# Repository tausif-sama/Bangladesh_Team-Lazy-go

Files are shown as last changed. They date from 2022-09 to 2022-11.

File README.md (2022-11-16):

# Engineering Documentation | Team Lazy-go | Bangladesh
----

This repository contains engineering materials of Lazy-bot, a self-driven vehicle's model from Team Lazy-go, Bangladesh, participating in the WRO Future Engineers competition in the season 2022.

----

## Team Members:

- Tausif Samin - email: <tausifsamin.dhk@gmail.com>, Discord: Ikigai#8742
- Iqbal Samin Prithul - email: <prithul0218@gmail.com>, Discord: Prithul#3957

----

## Repository Overview

+ `chassis` - this folder contains details of the chassis that we've used
+ `models` - contains 3D Printable files designed by us
+ `schemes` - contains the electrical systems schematics 
+ `src` - contains the main programs and control software and 
+ `t-photos` - contains one serious and one funny photo
+ `v-photos` - contains the photos of the robot from all required directions
+ `video` - contains youtube link of the video where you can see our robot in action
+ `others` - other essential photos

----

# Program arrangement and Algorithm Planning

The robot is running on an ESP32-based development board called the JRC board locally made in our country to run all the actuators and sense the environment. It is using the Huskylens to see the red/green obstacles as well as the corner lines (blue/orange). An MPU6050 gyroscope and accelerometer sensor are used to detect the orientation of the robot and count laps.

When the robot is first powered on with the battery, it initializes the chip and starts communicating with the Huskylens and IMU sensor. Once it is ready, the servo motor gets centered and it waits for the user to push the button. The code is then divided into three major parts - 

### Part 1 - Detecting run direction:

The first part determines the direction of the robot run. The robot moves slowly through the first straightforward section to ensure it can safely detect the direction of the run with its sonar sensors. Once it detects a large distance (>90cm) from one of the sensors, it marks the direction as “L” - clockwise, or “R”  - anti-clockwise accordingly.

### Part 2 - Completing the run as fast as possible:

In this part, we run a PID loop (1st round) or a proportional+obstacle avoiding code(2nd round) to complete the run as fast as possible. 

### **Wall avoidance:**

In the first round, we only check the sonar on the inner wall side (based on the direction of run detected from Part 1) to run a PID (proportional, integral, derivative) code. The code tries to keep the robot at a fixed distance from the wall while slowing down the rear axle drive motor whenever a turn is initiated.
To complete this part as fast as possible, we use smart algorithms to detect when the robot has just finished a turning section and is about to enter a straight section. The robot then spins the drive motor at maximum speed for a short period of time (40-50mS) to give the robot a great acceleration or “boost”.

In the 2nd round, however, we decided to disable the boost and changed PID control to just P or proportional to keep the robot centered on the track, which is sufficient at the slow speed of the robot.

### **Obstacle avoidance:**

When the huskylens detects an object, the ESP32 gets the object's color and location in the X and Y axis, as well as its height (to get the distance). The robot then follows the obstacle with an offset. Meaning it follows slightly on the right side of red obstacles, and slightly to the left of green obstacles. And once it reaches a distance of less than 30 cm, it turns the front wheel proportionally to the distance of the object (calculated from height) and the position of the object on the screen's horizontal axis.

### Wall collision protection:

If the robot detects a wall within 8cm of one of the sides, it rotates the servo in the other direction for a few milliseconds to keep the robot from hitting the wall.

### Part 3 - Detecting the end of 3 laps:

The robot equips a gyroscope sensor to measure the yaw angle by integrating the rotational acceleration values on the Z axis over time. Gyroscope sensors are infamous for drift in the angle over time, but our robot runs for such a short time that it does not affect its performance.

When the start button is pressed, the robot is at a zero-degree angle starting position. After each lap of the track, the robot spins 360 degrees. So we can detect the completion of three laps as soon as the robot completes 3x360 or 1080 degrees turn (+/- 20 degrees to compensate for errors). 
However, the robot is not instantly stopped, since it may not have reached the straightforward section. We start waiting for the Huskylens to detect a blue or orange line in front of it and stop instantly with a short backward pulse to the drive motor (hard break).

----

# Electrical Systems Design

We've carefully selected the best possible parts for our robot after several hundred hours of R&D and have tried to achieve highest possible efficiency and reliability. The electrical systems design is explained in the following paragraph.

## Parts List

+ JRC Board: An ESP32 based development board (Made in Bangladesh)
+ Huskylens: Embedded Vision Sensor
+ Adafruit HC-SR04 Ultrasonic Sensors
+ 12V 300RPM DC Geared Motor
+ 9imod DS20MG Servo Motor
+ VNH2SP30 Motor Driver
+ MPU6050
+ 2x MP1584 Buck Converter
+ Pololu U3V70A Boost Converter
+ 3S LiPo battery input through XT60 Connector

## Design decisions

+  JRC Board
    - We're using the JRC Board as it is equipped with an ESP-32 microcontroller at a clock speed of 240Hz. This is the fastest development platform for the price currently available. As the ESP-32 is dual-core, we can run two loops simaltaneously which is very benificial. 
    - There's a brief but impressive backsotry of the JRC Board. The abbreviation of 'JRC' is Jamilur Reza Chowdhury. Dr. Jamilur Reza Chowdhury was a Bangladeshi Civil Engineer, Professor, Researcher, and Education Advocate. He is also the pioneer of computers in Bangladesh and brought the first ever computers in Bangladesh. This board was designed and developed in the memory of Dr. Jamilur Reza Chowdhury to spread the light of IoT and hardware level electronics education to kids in Bangladesh.
- We're using the Huskylens which is an embedded machine vision sensor based on Kendryte K210 that can recognize and track colors and objects in real-time. We're using I2C to receive tracked color position data.
- We're using a 12V 500RPM geared motor with a modified gearbox that provides ample Torque and Speed to drive our car weiging about 900g.
- The front Axel is being articulated by a 9imod DS20MG Servo Motor. This Servo boasts a coreless motor inside and operates at a speed of 0.09sec/60°@7.4V.
- We've used a VNH2SP30 Motor driver replacing a TB6612FNG because of lack of current. VNH2SP30 has no problems communicating with the 3.3v ESP-32 and provides ample current to the motor.
- We're using 2x HC-SR04 sonar sensors to measure distance from both the left and right walls.
- The Pololu U3V70A Boost Converter was used because providing sustained voltage to the motor driver is an absolute necessity for achieving consistent performance. U3V70A Provides a constant 12v to the Motor driver regardless of the battery voltage.
- 2x MP1584 buck converters were used, one for powering all the 5v peripherals and on-board devices and the other one for providing 7.4v to the servo motor.
- A MPU6050 was used to know the orientation of the robot in real-time. This data is later used to count laps.
- A 3S 12.6V 1500mAh battery is powering this entire system. We're getting a runtime of average 3 hours.

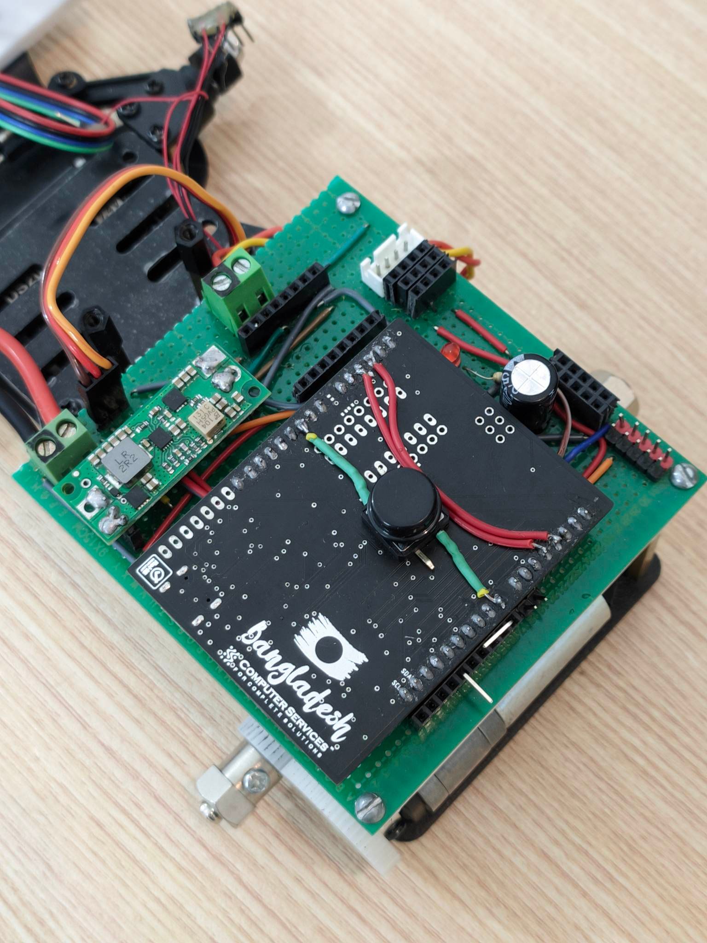
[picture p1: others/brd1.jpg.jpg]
brd1

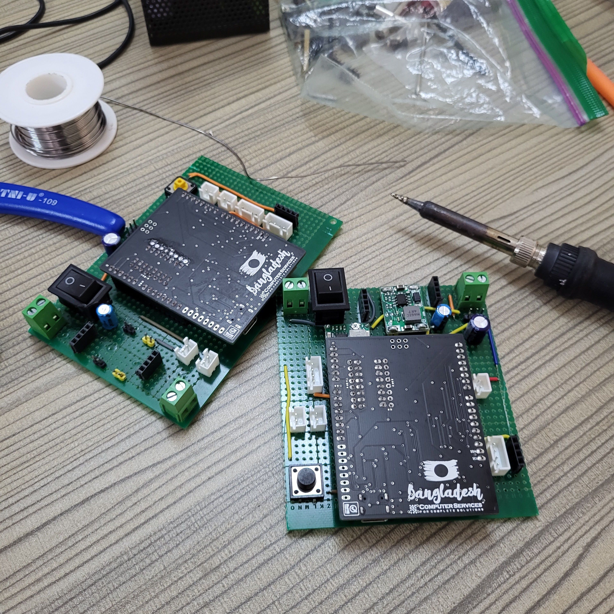
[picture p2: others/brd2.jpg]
brd2


----

# Mechanical Design

We're using a ready made Ackermann based chassis kit from YF robot and have significantly modified each aspect of the chassis. The chassis base plate is made of Aluminum and the rest of the parts involve brass spacers, acrylic top plates, front articulating axel parts and some other miscellaneous parts. We've also designed and 3D Printed some parts for making our chassis more practical.

## Design Decisions
We setteled on the YF Robot chassis because it provided a robust platform to work on and featured ackermann steering mechanism. We've deigned and 3D printed some parts which were required for the optimal operation of the robot. 

## 3D Printed parts designed by us

- We've designed a sonar mount which is mounted in the front of the robot where the sonar sensors are mounted at an angle of 20 deg. We've tested this to be the optimal angle for the sonars to detect walls before hand, providing ample time for the bot to react.
- An elevated and angled mount for the huskylens was designed for the camera to get optimal vision of the track.
- The wheels were completely 3D printed, except for the tires. After extensive testing, we've found that thin twheels perfom better in cases where precise movement is required.
- A mounting plate for the veroboard was designed so that the solder joints under the board do not make any contact with the motor.

----

# Software Setup
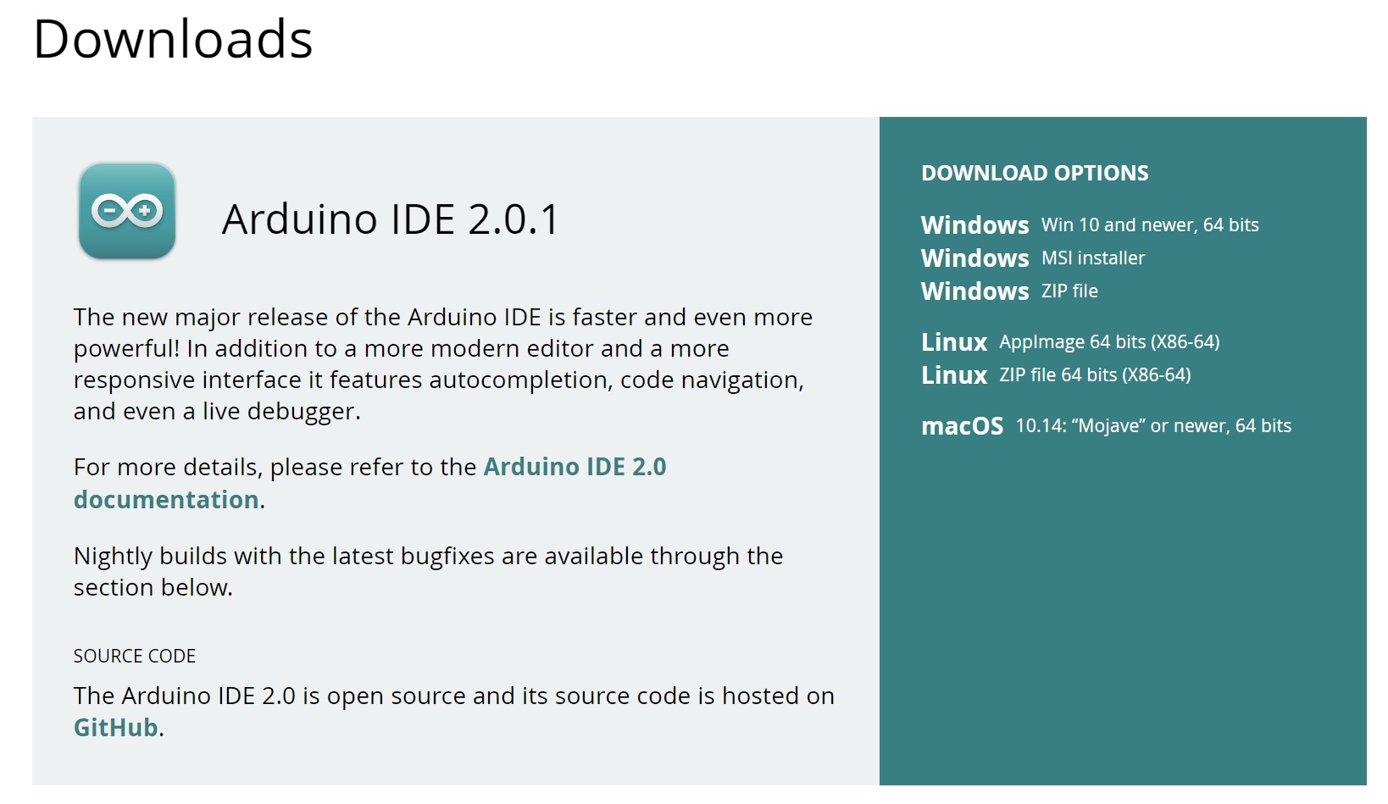
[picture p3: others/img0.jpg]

- First we need to install the latest Arduino IDE on our computer from: arduino.cc/en/Main/Software. If you already have an older version, uninstall it and install the latest one again. Otherwise, it may not work.

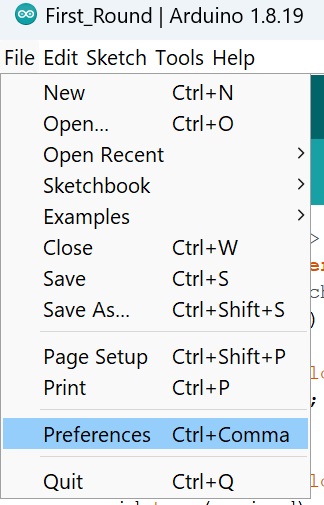
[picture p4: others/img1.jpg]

- In your Arduino IDE, go to File > Preferences, and enter the following into the "Additional Board Manager URLs" field, and click OK:
`https://raw.githubusercontent.com/espressif/arduino-esp32/gh-pages/package_esp32_index.json`

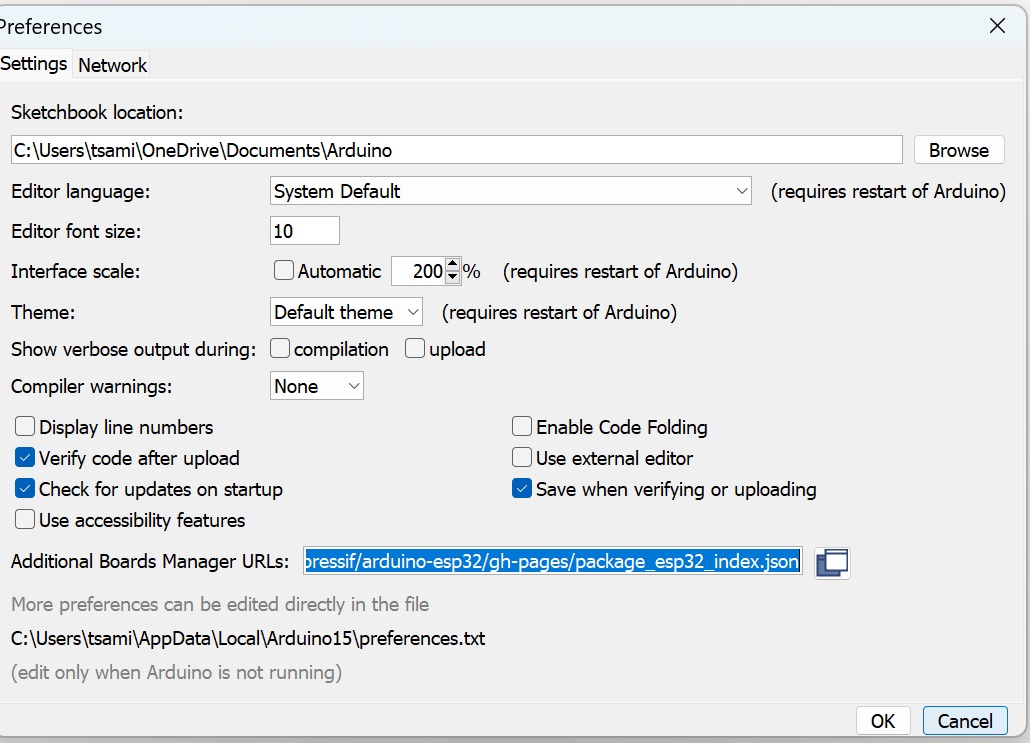
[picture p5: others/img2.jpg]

- Open the Arduino Boards Manager: Tools > Board > Boards Manager... and search for ESP32. Press install button for the "ESP32 by Espressif Systems".

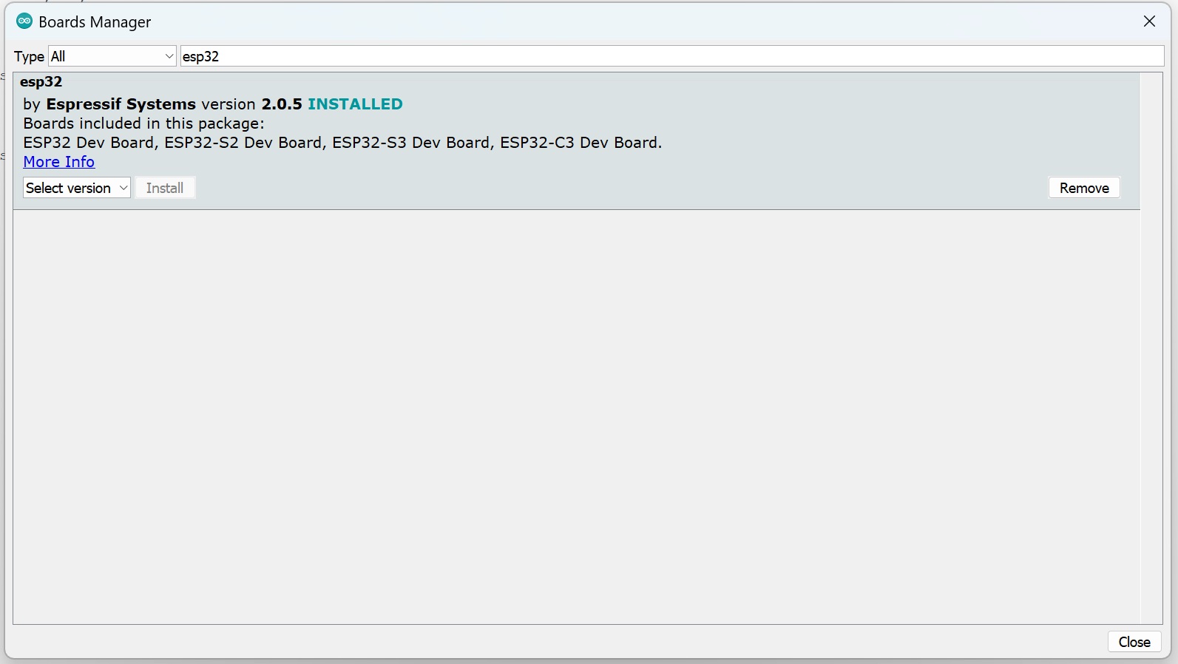
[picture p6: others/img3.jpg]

- Now we try to upload our code to the ESP32. Select your Board in Tools > Board menu (in our case it is the DOIT ESP32 DEVKIT V1).

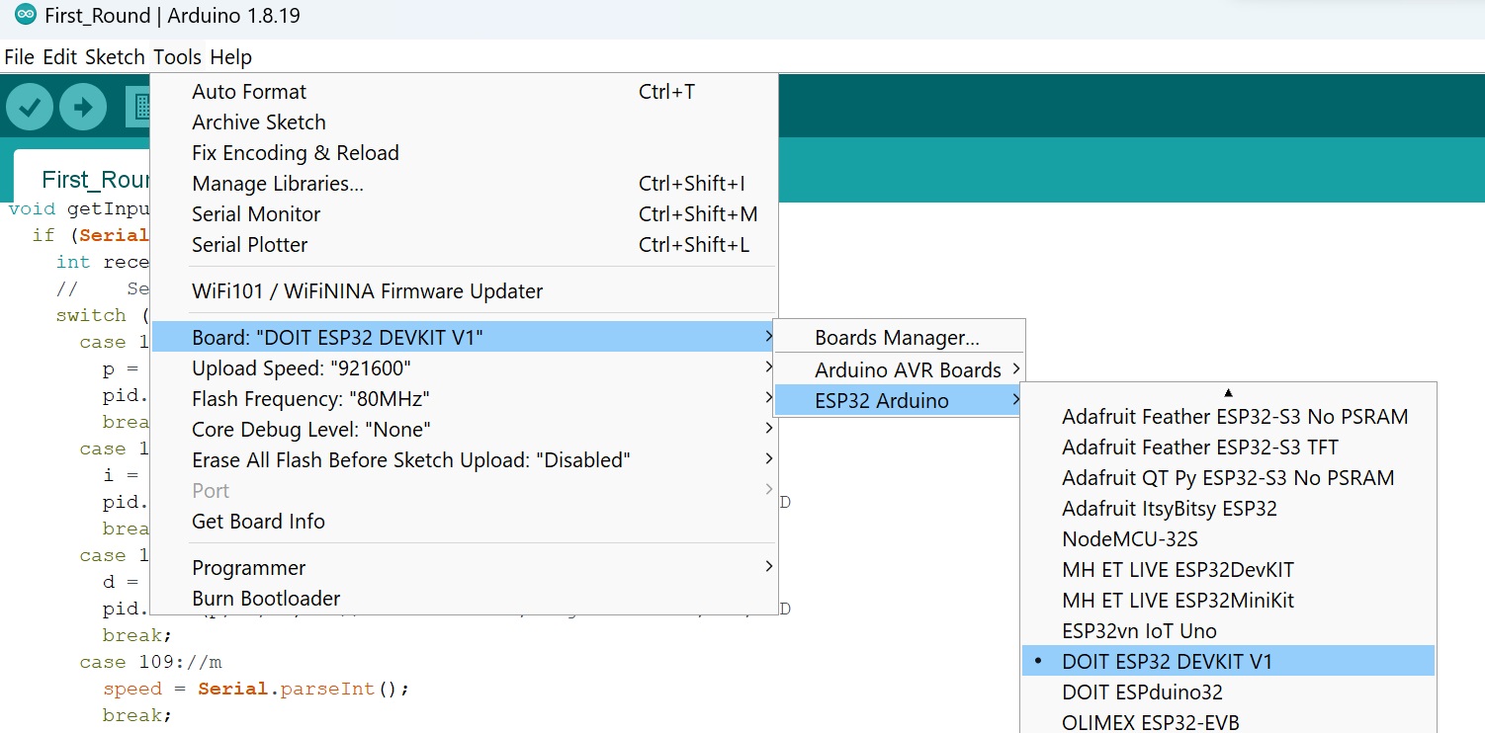
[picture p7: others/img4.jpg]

- Select the COM port, and open the sketch.

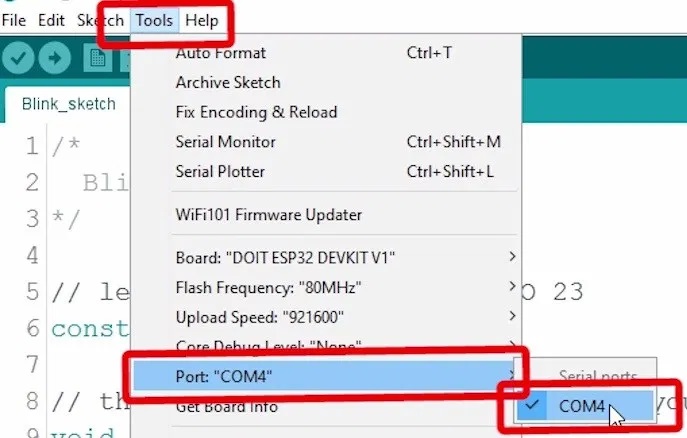
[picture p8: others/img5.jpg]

- Press the Upload button in the Arduino IDE. Wait a few seconds while the code compiles and uploads to your board. It should say "Done Uploading" if the upload completes successfully.

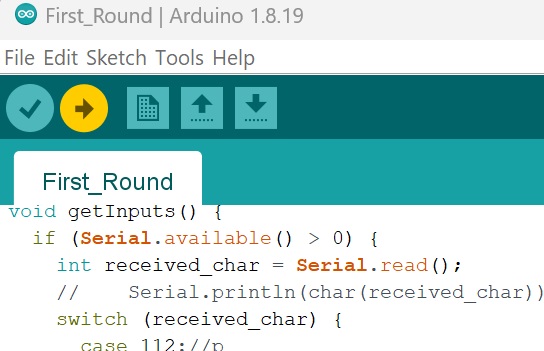
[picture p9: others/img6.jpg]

- Now you can place the robot on the track, power it up, and wait until the front servo centers.

- Press the button and it will start doing the laps.

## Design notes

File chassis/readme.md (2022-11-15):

Main Chassis 
====

We're using a ready made Ackermann based chassis kit from YF robot and have significantly modified each aspect of the chassis. The chassis base plate is made of Aluminum and the rest of the parts involve brass spacers, acrylic top plates, front articulating axel parts and some other miscellaneous parts.

## Chassis files Overview

   - `baring placement`: This shows the unique chassis's bearing arrangement on the front axel wheels.
   - `chassis parts list`: This shows the number of parts and the kit contains.
   - `chassis.png`: Shows overall image of the chassis
   - `front axel wheels assembly`: This shows the assembly mechanism of the front axel.
   - `front axel.png`: This shows the placement of the front steering mechanism on the baseplate
   - `main motor.png`: This shows the placement of the motor and it's mounting mechanism on the baseplate.
   - `servo.png`: This shows the placement of the servo motor and it's mounting mechanism with the linkages.

Please refer to `models` for the 3D Printed Parts.

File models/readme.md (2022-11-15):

Designed and 3D Printed Models
====

These are all the essential parts of our robot which was 3D Printed. All the parts were modeled and designed in Autodesk Fusion 360 and printed with a self-made custom 3D Printer.

## 3D Printable files overview

   - `Motor Driver Mount.stl`: This model helps us mount the VNH2SP30 Motor Driver to the chassis.
   - `PCB mounting plate.stl`: This model is used to mount our veroboard to the robot.
   - `Sonar mount 20 degree.stl`: This model is used to mount our front two sensors at an angle.
   - `Wheel A.stl`: All our wheels are fully 3D Printed. This model is one part of the wheel.s
   - `Wheel B.stl`: All our wheels are fully 3D Printed. This model is the other of the wheel.
   - `Older designs`: This file contains older iterations of our models.

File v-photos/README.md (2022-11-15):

Electrical Systems Design
====

Folder contains photos of the lazy-bot from all required directions

## Overview

   - `front.jpg`: front view: features 3D Printed sonar mount, donar connection daughter board, battery and front steering axels.
   - `back.jpg`: back view: features motor, gears, 
   - `top.jpg`: top view: veroboard, JRC Board, huskylens with wide angle clip-on lens adapter, and other electronic parts
   - `bottom.jpg`: bottom view: aluminium base plate
   - `left.jpg`: view from left
   - `right.jpg`: view from right

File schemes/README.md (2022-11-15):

Electrical Systems Design
====

Folder contains the electrical design schematics, designed in EasyEDA.

## Overview

   - `Schematic_Lazy-bot_v0.1.4.json`: this json file can be imported in EasyEDA to edit and make changes.
   - `Schematic_Lazy-bot_v0.1.4.pdf`: this is the pdf of the schematic, good for printing purposes.
   - `Schematic_Lazy-bot_v0.1.4.png`: this is the image of the schematic.
   - `Schematic_Lazy-bot_v0.1.4.schdoc`: this can be imported to Altium Designer
   - `Schematic_Lazy-bot_v0.1.4.svg`: this is the svg of the schematic, good for online publishing.

## Parts List

+ JRC Board: An ESP32 based development board (Made in Bangladesh)
+ Huskylens: Embedded Vision Sensor
+ Adafruit HC-SR04 Ultrasonic Sensors
+ 12V DC Geared Motor
+ 9imod DS20MG Servo Motor
+ VNH2SP30 Motor Driver
+ MPU6050
+ 2x MP1584 Buck Converter
+ Pololu U3V70A Boost Converter
+ 3S LiPo battery output through XT60 Connector

## Electrical Schematics Explanation

- Connections
   - We've shorted the TRIG and ECHO pin of each sonar and using only one wire to communicate with the Sonar. This reduces clutter without any performance loss whatsoever.
   - Huskylens and MPU6050 are connected via I2C to the JRC Board.
   - The servo signal is connected to GPIO 4.
   - VNH2SP30 is connected to the JRC board through a jumper pins, where: INA, INB, PWM, EN are connected to GPIO 25, 26, 2 and 33 respectively.
   - A push button is connected to PIN 32, when the button is pressed, the PIN is pulled down to ground.
   - All the spare GPIO are laid out on a female header for convenience.
- PSU
   - We're using two MP1584 so that we can use our servo at our full potential, i.e 0.09sec/60°@7.4V. Two MP1584 provides ample current to all of the onboard peripherals.
   - U1: MP1584EN Provides 7.4v to the servo.
   - U4: MP1584EN Provides 5v to the the all 5v devices on board.
   - Pololu U3V70A is receiving power from the battery at about 11.1V and later keeping the voltage constant at 12V for the motor.
   - The BATT_IN hoasts a solid XT60 connector for the battery input. 
   - All connections and solder joints are reinforced for high current demand scenarios.
- Board
    - We're using the JRC Board as it is equipped with an ESP-32 microcontroller at a clock speed of 240Hz. This is the fastest development platform for the price currently available. As the ESP-32 is dual-core, we can run two loops simaltaneously which is very benificial. 
    - There's a brief but impressive backsotry of the JRC Board. The abbreviation of 'JRC' is Jamilur Reza Chowdhury. Dr. Jamilur Reza Chowdhury was a Bangladeshi Civil Engineer, Professor, Researcher, and Education Advocate. He is also the pioneer of computers in Bangladesh and brought the first ever computers in Bangladesh. This board was designed and developed in the memory of Dr. Jamilur Reza Chowdhury to spread the light of IoT and hardware level electronics education to kids in Bangladesh. We're joining in to support their cause out of respect for Dr. Jamiulur Reza Chowdhury Sir and spreding the love for robotics and electronics throughout Bangladesh.
    
## Steps to replicate the exact same electrical design

+  Replicating the Power system
    - Connect the main power from the XT60 connector to the both MP1584 buck converters and U3V70A Boost Converter. Set the output voltage of the boost converter to 12v (Whatever voltage your motor needs) and one MP1584 to 7.4v for the servo and the other one to 5V for all of the other onboard 5v devices.
    - Connect the Output of the U3V70A to the PWR_IN and GND Pins of the VNH2SP30 Motor Driver.

+  Connecting all the logic wires
    - We're communicating with the huskylens and MPU6050 through I2C, connecting SDA and SCL of the JRC Board to the respective SCL and SDA Pins of MPU6050 and huskylens.
    - We're taking sonar input on digital pins 16, 17.
    - VNH2SP30 INA, INB, PWM, EN are connected to pins 25, 26, 2 and 33 respectively.
    - A push button is wired to pin 32 and ground.
    - Servo Signal pin to GPIO 4.
    - Please follow the Schematics for detailed wiring guidelines.

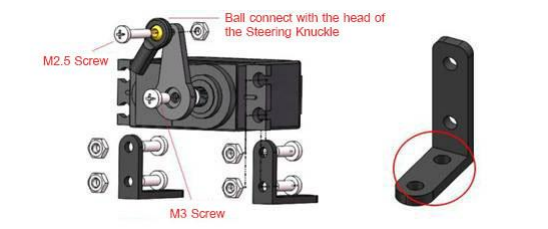
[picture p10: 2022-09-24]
chassis/servo.png

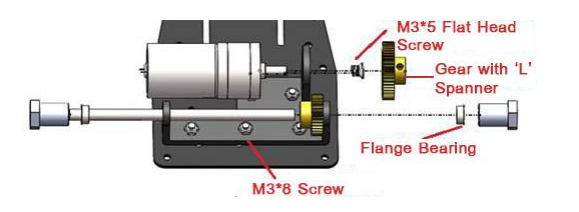
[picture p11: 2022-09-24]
chassis/main motor.png

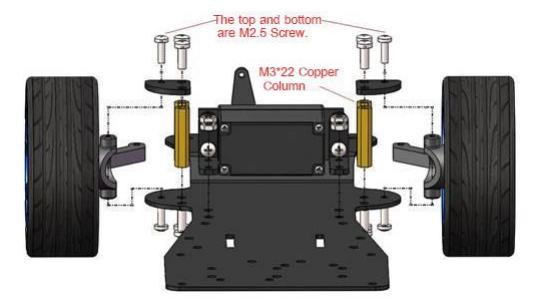
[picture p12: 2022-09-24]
chassis/front axel.png

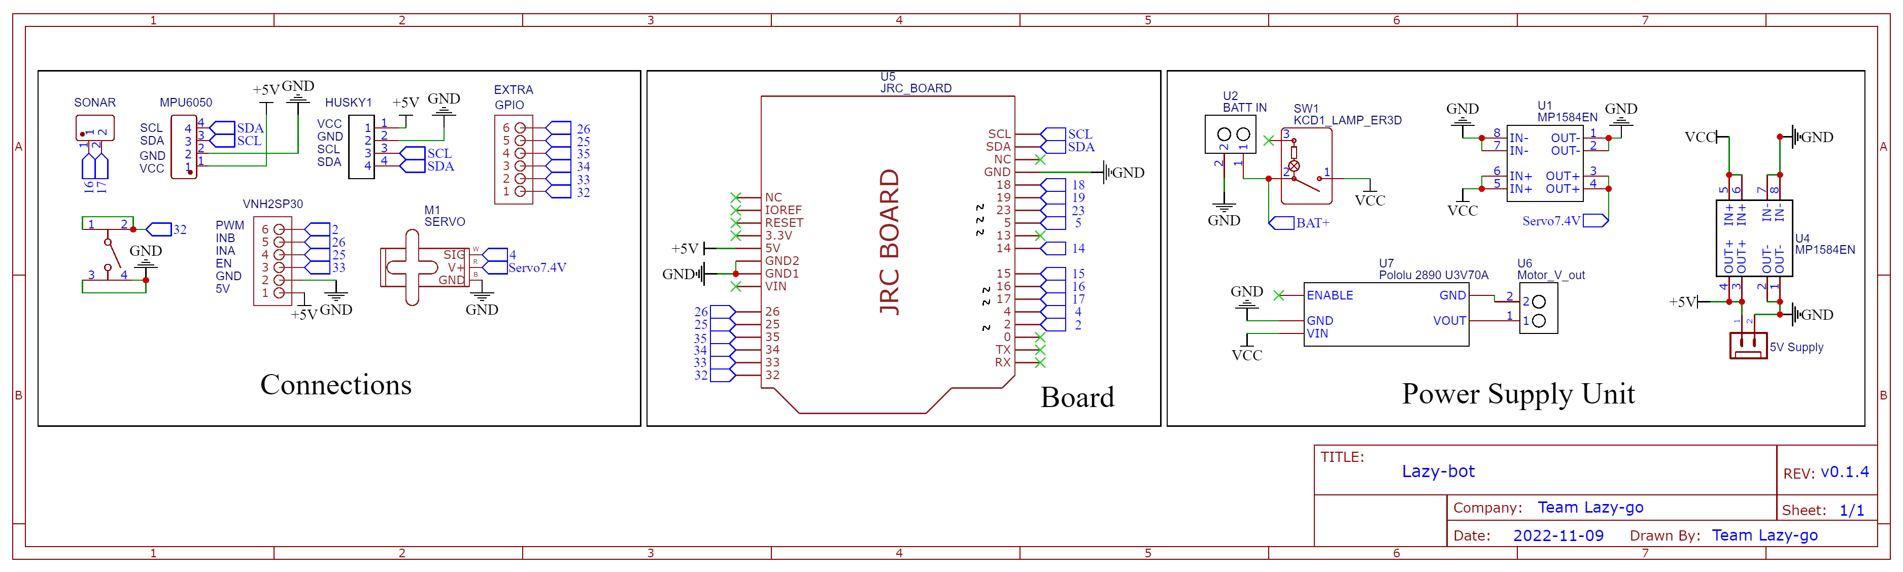
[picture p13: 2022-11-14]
schemes/Schematic_Lazy-bot_v0.1.4.png

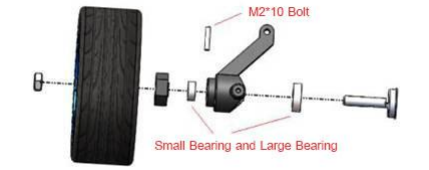
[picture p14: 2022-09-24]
chassis/baring placement.png

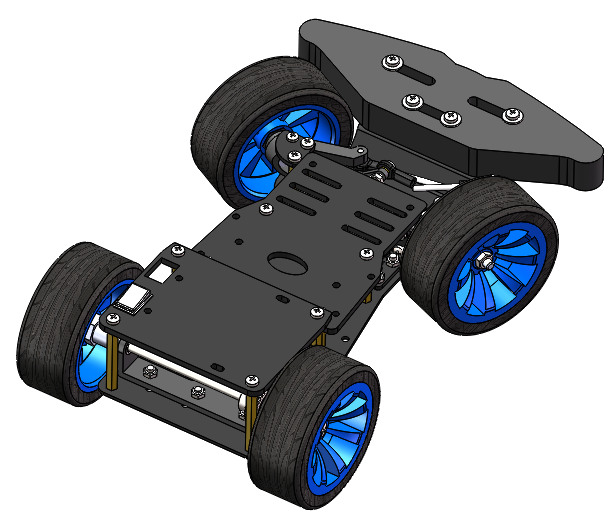
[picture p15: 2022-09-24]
chassis/chassis.png

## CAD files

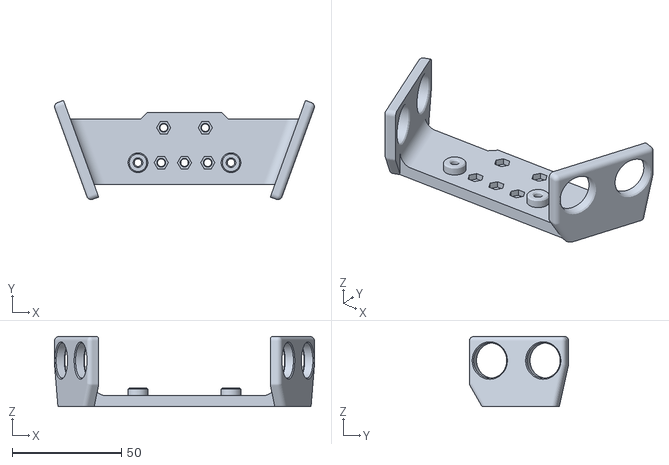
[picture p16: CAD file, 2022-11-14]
models/Sonar mount 20 degree.stl
118.8 x 45.3 x 32.0

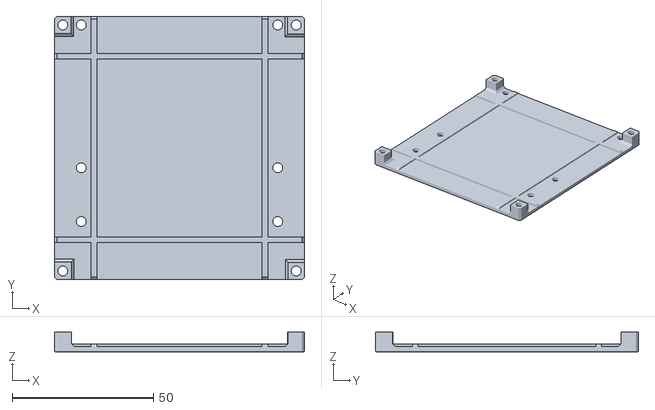
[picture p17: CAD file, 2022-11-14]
models/PCB mounting plate.stl
88.5 x 93.0 x 7.00

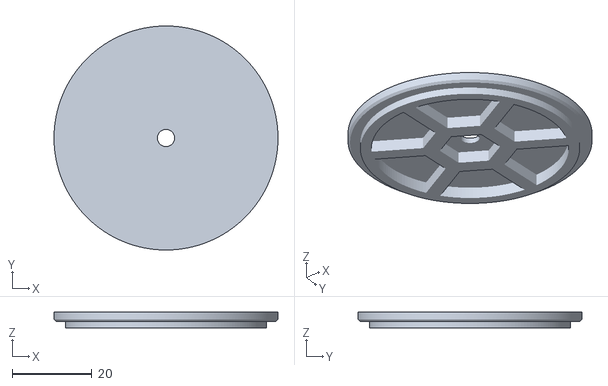
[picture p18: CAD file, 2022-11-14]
models/Wheel A.stl
56.0 x 56.0 x 4.00

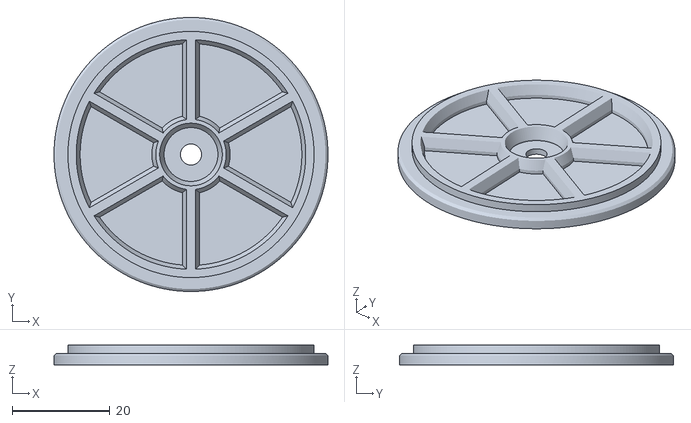
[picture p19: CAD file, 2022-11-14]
models/Wheel B.stl
56.0 x 56.0 x 4.00

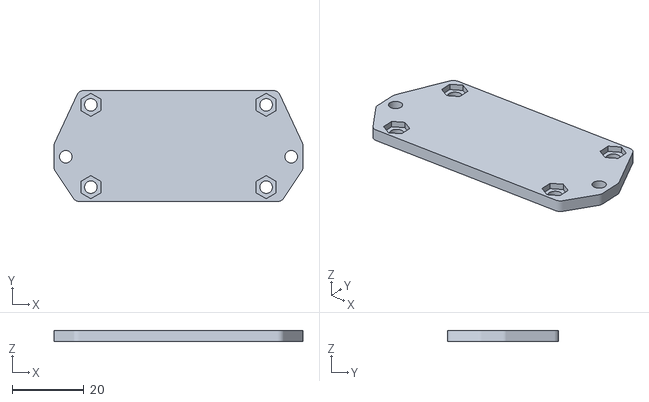
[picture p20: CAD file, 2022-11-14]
models/Motor Driver Mount.stl
69.6 x 31.0 x 3.00

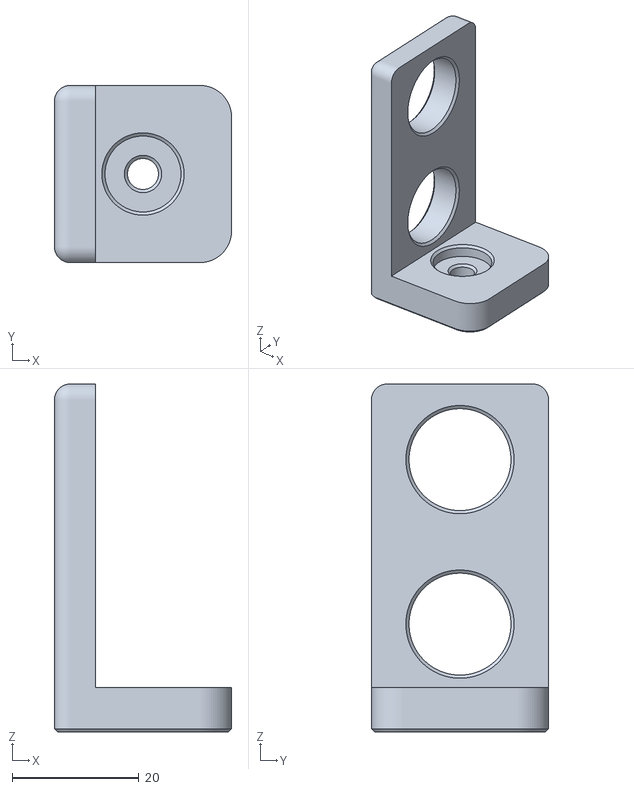
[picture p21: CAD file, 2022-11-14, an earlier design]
models/Older designs/Sonar mount.stl
28.0 x 28.0 x 55.0

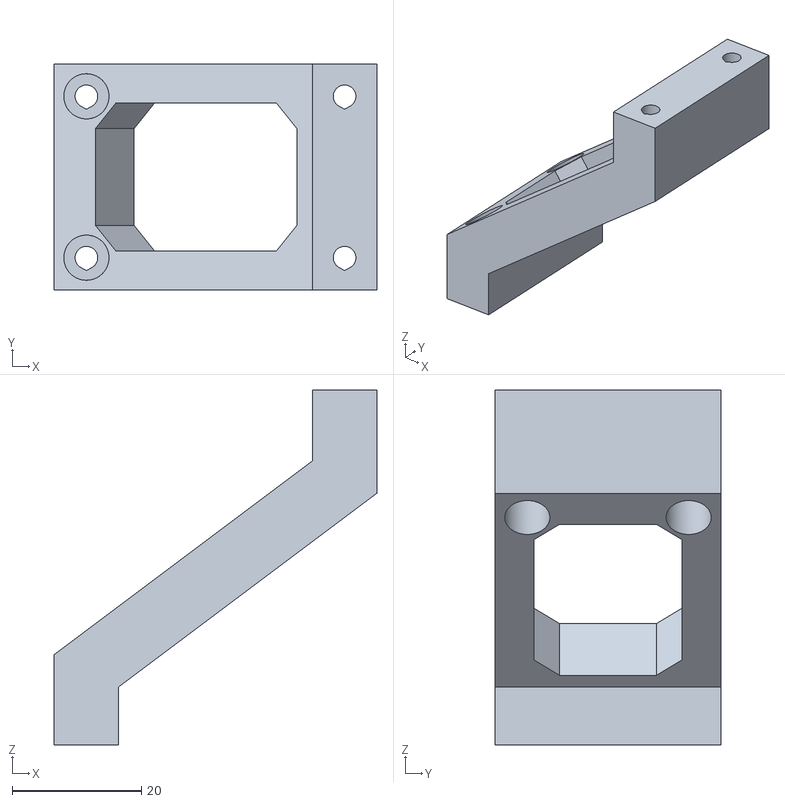
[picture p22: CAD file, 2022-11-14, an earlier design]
models/Older designs/Huskylens extended mount.stl
50.0 x 35.0 x 55.0

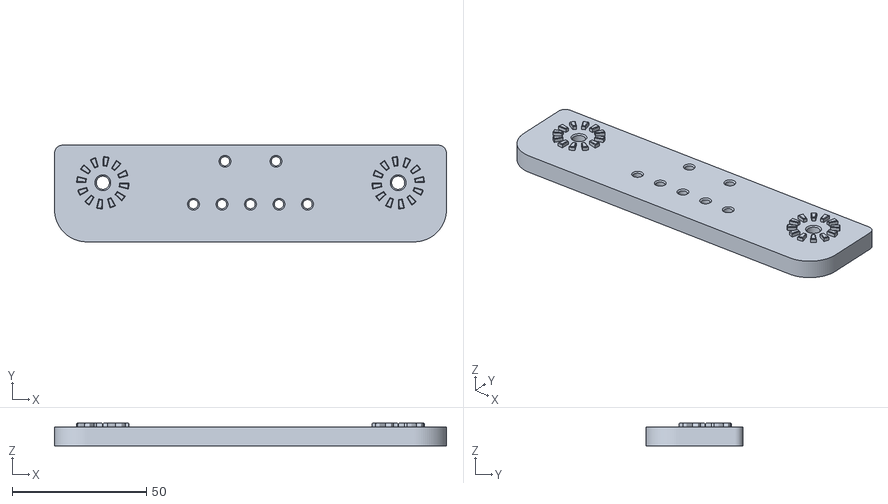
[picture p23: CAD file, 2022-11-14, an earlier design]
models/Older designs/Sonar mount base.stl
146.0 x 36.0 x 8.50

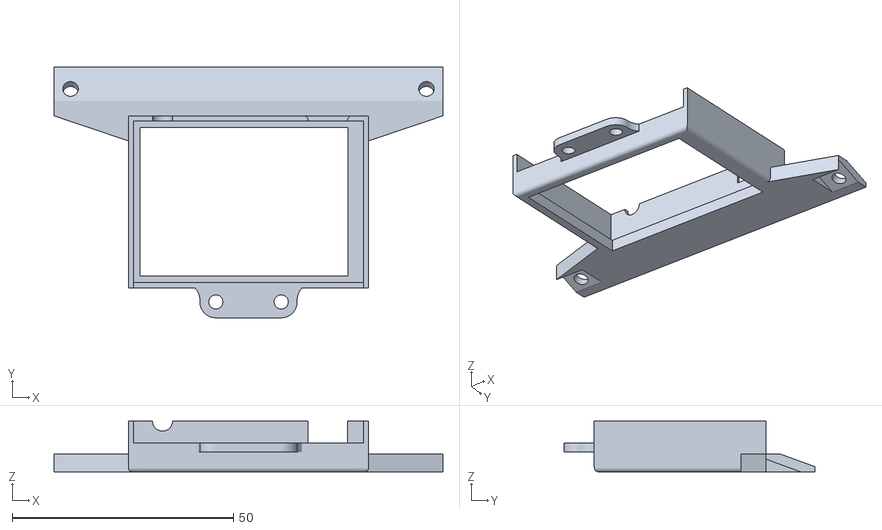
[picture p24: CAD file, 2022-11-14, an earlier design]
models/Older designs/Huskylens LED mount.stl
88.0 x 56.7 x 11.5

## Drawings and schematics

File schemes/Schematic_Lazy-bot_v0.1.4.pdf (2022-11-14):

# U5 JRC BOARD

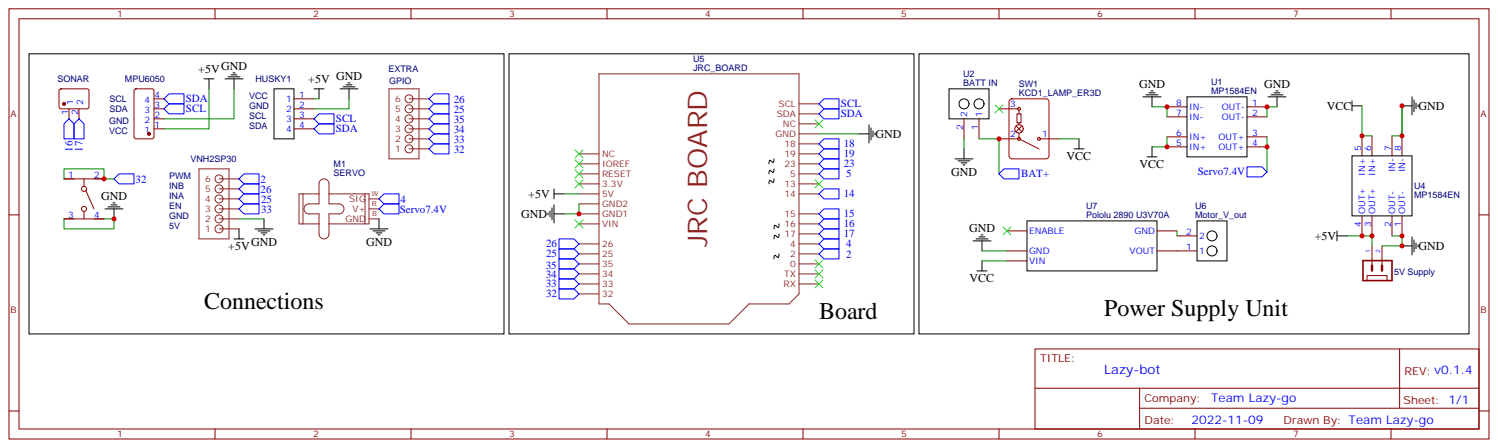
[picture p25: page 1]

Company: Team Lazy-go

Drawn By: Team Lazy-go

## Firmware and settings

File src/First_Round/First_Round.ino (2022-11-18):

#include <NewPing.h>
#include <PIDController.h>
#include <ESP32Servo.h>
#include <HUSKYLENS.h>
#include <MPU6050_light.h>
MPU6050 mpu(Wire);
int yawAngle = 0, startAngle = 0;
#define endAngle 1080
unsigned long MPUtimer = 0, lapTimer = 0;

Servo myservo;
#define MAX_DISTANCE 200 // Maximum distance (in cm) to ping.
PIDController pid; // Create an instance of the PID controller class, called "pid"
HUSKYLENS huskylens;


NewPing sonarL(15, 15, MAX_DISTANCE), sonarR(16, 16, MAX_DISTANCE);     // 2 = right sensor, 3 = left
#define IN1 4
#define IN2 25
#define PWM 2
#define stdby 26
#define servo 33
#define button 14

int mainSpeed = 120;
bool start = false;
int dif, ID;
int angle;
int cal, pwm;
long duration, distance, RD, FD, LD;
int turndis = 110;
char dir;
float p = 25, i = .1, d = 8;


int sensorValue, output, lastOutput;
unsigned long lastMillis = 0, zeroStartMillis = 0, highSpeedMillis = 0, lastTurnMillis = 0, stopMillis = 0;
float alpha = 0.6;
int speed = 120;
bool justTurned = false;
byte turnCount = 0, orangeCount = 0, blueCount = 0;
int timeToIgnore = 1000;

void setup () {
  Serial.begin(115200);  // Some methods require the Serial.begin() method to be called first'
  //Serial.begin("ESP32test");  // Some methods require the Serial.begin() method to be called first'

  pinMode(IN1, OUTPUT);
  pinMode(IN2, OUTPUT);
  pinMode(PWM, OUTPUT);
  pinMode(stdby, OUTPUT);
  pinMode(button, INPUT_PULLUP);

  Wire.begin();
  while (mpu.begin() != 0) {
    Serial.print(F("MPU6050 failed to initialize!"));
  }
  mpu.calcOffsets(); // gyro and accelero
  lapTimer = millis();
  while (!huskylens.begin(Wire))
  {
    Serial.println(F("Begin failed!"));
    Serial.println(F("1.Please recheck the \"Protocol Type\" in HUSKYLENS (General Settings>>Protocol Type>>I2C)"));
    Serial.println(F("2.Please recheck the connection."));
    delay(100);
  }


  pid.begin();          // initialize the PID instance
  pid.setpoint(29);    // The "goal" the PID controller tries to "reach"
  pid.tune(p, i, d);  // Tune the PID, arguments: kP, kI, kD
  myservo.attach(servo);
  myservo.write(90); // 50, 90, 140
  dir = 'L';
  waitForN();
  drive(70);
  byte leftCount = 0, rightCount = 0;
  while (1) {
    MPU();
    delay(2);
    LD = sonarL.ping_cm();
    if (LD == 0 || LD > 200) {
      leftCount++;
      LD = MAX_DISTANCE;
    }
    RD = sonarR.ping_cm();
    if (RD == 0 || RD > 200) {
      rightCount++;
      RD = MAX_DISTANCE;
    }
    if (leftCount > 10) {
      dir = 'L';
      break;
    }
    if (rightCount > 10) {
      dir = 'R';
      break;
    }
    int error = LD - RD;
    myservo.write(constrain(map(error, -80, 80, 50, 140), 50, 140));
    //    Serial.print(LD);
    //    Serial.print("    ");
    //    Serial.print(RD);
    //    Serial.print("    ");
    //    Serial.println(error);
    //    if (huskylens.request(3) || huskylens.request(4)) {
    //      if (huskylens.count(3) > 0 || huskylens.count(4) > 0) {
    //        turnCount++;
    //        lastTurnMillis = millis();
    //        justTurned = true;
    //        //        break;
    //      }
    //    }
  }
}
int endAngleReached = 0;
void loop () {
  MPU();
  if (yawAngle > endAngle - 18 && yawAngle < endAngle + 18) {
    endAngleReached++;
  }
  if (endAngleReached > 5 && (huskylens.request(3) || huskylens.request(4))) {
//    if (huskylens.count(3) > 0 || huskylens.count(4) > 0) {
      myservo.write(90);
      drive(-150);
      delay(100);
      drive(0);
      Serial.println("3 laps completed!\n");
      Serial.print("Lap time: ");
      int lapTime = (millis() - lapTimer) / 1000;
      Serial.print(lapTime);
      Serial.println(" seconds");
      while (1);
//    }
  }
  if (justTurned == true && abs(output) < 15) {
    Serial.println("\nSpeeding up!");
    if (turnCount < 12)speed = 255;
    highSpeedMillis = millis();
    justTurned = false;
  }
  if (millis() - highSpeedMillis > 50 && speed > mainSpeed) {
    speed = mainSpeed;
  }
  //  if (turnCount >= 12) {
  //    myservo.write(95);
  //    drive(-200);
  //    delay(100);
  //    drive(0);
  //    while (turnCount != 0) {
  //      getInputs();
  //    }
  //  }
  delay(1);
  //   pid.setpoint(19);
  //  Serial.print(dir);
  //  Serial.print("\t");
  //  Serial.print(sensorValue);
  //  Serial.print("\t");
  //  Serial.print(output);
  //  Serial.print("\t");
  //  Serial.print(orangeCount);
  //  Serial.print("\t");
  //  Serial.print(blueCount);
  //  Serial.print("\t");
  //  Serial.print(turnCount);
  //  Serial.print("\t");


  if (dir == 'R') {
    pid.limit(-40, 50);   // Limit the PID output between 0 and 255, this is important to get rid of integral windup!
    RD = sonarR.ping_cm();
    if (RD == 0) {
      RD = MAX_DISTANCE;
      drive(60);
      delay(2);
    }

    sensorValue = RD;  // Read the value from the sensor
    output = pid.compute(sensorValue);   // Let the PID compute the value, returns the optimal output
    output = constrain(output, -40, 50);

    myservo.write(92 + output);
    if (turnCount > 11) {
      drive(speed);
    } else {
      drive(speed - (abs(output) * 1.3));
    }
  } else {
    pid.limit(-50, 40);   // Limit the PID output between 0 and 255, this is important to get rid of integral windup!
    LD = sonarL.ping_cm();
    if (LD == 0) {
      LD = MAX_DISTANCE;
      drive(60);
      delay(2);
    }
    //    else
    //      sensorValue = alpha * LD + (1 - alpha) * sensorValue;
    sensorValue = LD;
    output = pid.compute(sensorValue);   // Let the PID compute the value, returns the optimal output
    output = constrain(output, -50, 40);

    myservo.write(92 - output);
    if (turnCount > 11) {
      drive(speed);
    } else {
      drive(speed - (abs(output) * 1.3));
    }
  }

  if (sensorValue > 120 && millis() - lastTurnMillis > 1000) {
    turnCount++;
    lastTurnMillis = millis();
    justTurned = true;
  }
  if (turnCount > 11) {
    mainSpeed = 80;
    speed = mainSpeed;
  }

  Serial.println(yawAngle);
  //  const float alpha2 = 0.9;
  //  output = alpha2 * output + (1 - alpha2) * lastOutput;
  //  lastOutput = output;
  /*if(LD>RD && LD>170)
    {
      myservo.write(104-60);
      drive(190);
      delay(700);
      myservo.write(104+60);
      drive(190);
      delay(220);
    } */

  //  Serial.print("RD = ");
  //  Serial.print(RD);
  //  Serial.print(" - ");
  //  Serial.print("LD = ");
  //  Serial.print(LD);
  //  Serial.print(" - ");
  //  Serial.print("PID OUTPUT=");
  //  Serial.println(output);

  /* if(output<-25){
     myservo.write(104-40);
     drive(255);
     //delay(1500);
     myservo.write(104+40);
     drive(200);
     //delay(1000);
     myservo.write(104);
    }

    else (FD<10){
     drive(0);
    }    */

  Serial.println(millis() - lastMillis);
  lastMillis = millis();
  getInputs();
}




void drive(int pwm) {
  if (pwm < 0) {
    digitalWrite(IN1, LOW);
    digitalWrite(IN2, HIGH);
    analogWrite(PWM, constrain(abs(pwm), 0, 255));
    digitalWrite(stdby, HIGH);
  } else if (pwm > 0) {
    digitalWrite(IN1, HIGH);
    digitalWrite(IN2, LOW);
    analogWrite(PWM, constrain(abs(pwm), 0, 255));
    digitalWrite(stdby, HIGH);
  } else {
    digitalWrite(IN1, LOW);
    digitalWrite(IN2, LOW);
    analogWrite(PWM, pwm);
    digitalWrite(stdby, HIGH);
  }
}

void getInputs() {
  if (Serial.available() > 0) {
    int received_char = Serial.read();
    //    Serial.println(char(received_char));
    switch (received_char) {
      case 112://p
        p = Serial.parseFloat();
        pid.tune(p, i, d);  // Tune the PID, arguments: kP, kI, kD
        break;
      case 105://i
        i = Serial.parseFloat();
        pid.tune(p, i, d);  // Tune the PID, arguments: kP, kI, kD
        break;
      case 100://d
        d = Serial.parseFloat();
        pid.tune(p, i, d);  // Tune the PID, arguments: kP, kI, kD
        break;
      case 109://m
        speed = Serial.parseInt();
        break;
      case 110://n
        if (start != true) {
          //          startAngle = abs(mpu.getAngleZ());
          lapTimer = millis();
          drive(150);
          delay(50);
          start = true;
        }
        break;
      case 111://o
        ESP.restart();
        break;

      case 113://q
        timeToIgnore = Serial.parseInt();
        Serial.print("set to: ");
        Serial.println(timeToIgnore);
        break;

      case 114://r
        Serial.print("Current degree");
        Serial.println(yawAngle);
        drive(-200);
        delay(100);
        drive(0);
        waitForN();
        break;
    }
  }
}

void MPU() {
  mpu.update();
  if ((millis() - MPUtimer) > 50) {
    if (start == false) {
      startAngle = abs(mpu.getAngleZ());
      Serial.println(startAngle);
    } else {
      yawAngle = abs(mpu.getAngleZ()) - startAngle;
    }
    MPUtimer = millis();
  }
}

void waitForN() {
  while (start == false) {
    MPU();
    //    startAngle = abs(mpu.getAngleZ());
    getInputs();
    if (digitalRead(button) == LOW) {
      //          startAngle = abs(mpu.getAngleZ());
      lapTimer = millis();
      drive(150);
      delay(50);
      start = true;
    }
  }
}

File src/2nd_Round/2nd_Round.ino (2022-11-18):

int autoSteer(char h) {
  int minDist = 2, maxDist, minAng, maxAng;
  int distance, wallPos, err, lasterr = 0, P, D, ang;
  maxDist = (wallDist - minDist) * 2;
  //  maxDist = 76;
  minAng = mid_pos - max_steering;
  maxAng = mid_pos + max_steering;
  if (h == 'R')distance = sonarR.ping_cm();
  else distance = sonarL.ping_cm();
  if (distance == 0) distance = 200;
  //  Serial.print("min dist: ");
  //  Serial.print(minDist);
  //  Serial.print("  max dist: ");
  //  Serial.print(maxDist);
  //  Serial.print("min ang: ");
  //  Serial.print(minAng);
  //  Serial.print("  max ang: ");
  //  Serial.print(mid_pos);
  //  Serial.print("  Sonar: ");
  //  Serial.print(distance);
  if (distance < minDist && distance != 0)distance = minDist;
  if (distance > maxDist || distance == 0)distance = maxDist;
  Serial.print(distance);

  if (firstIntersection == true) {
    MPU();
    delay(2);
    int LD = sonarL.ping_cm();
    if (LD == 0 || LD > 100) {
      leftCount++;
      LD = MAX_DISTANCE;
    }
    int RD = sonarR.ping_cm();
    if (RD == 0 || RD > 100) {
      rightCount++;
      RD = MAX_DISTANCE;
    }
    if (leftCount > 10) {
      firstIntersection = false;
      dir = 'L';
    }
    if (rightCount > 10) {
      firstIntersection = false;
      dir = 'R';
    }
    int error = LD - RD;
    ang = constrain(map(error, -80, 80, 50, 140), 50, 140);
  } else {
    //  if (distance == 0 || distance > 100) distance = 300;
    if (h == 'R') {
      ang = constrain(map(distance, minDist, maxDist, maxAng, minAng), 48, 142);
      if (distance == maxDist)
        ang = 55;
    } else {
      ang = constrain(map(distance, minDist, maxDist, minAng, maxAng), 48, 142);
      if (distance == maxDist)
        ang = 142-5;
    }
  }
  myservo.write(ang);
  delay(10);
  return map(ang, mid_pos - max_steering, mid_pos + max_steering, -32, 40);
}
